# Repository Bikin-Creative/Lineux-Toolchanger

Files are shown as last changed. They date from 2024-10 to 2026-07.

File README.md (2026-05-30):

# Lineux-Toolchanger
### Toolchanger for fdm 3d printers
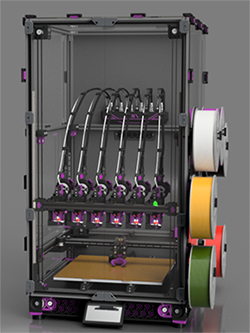
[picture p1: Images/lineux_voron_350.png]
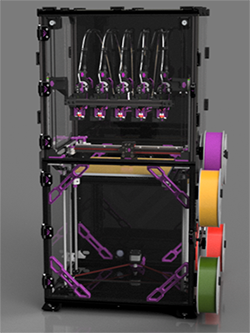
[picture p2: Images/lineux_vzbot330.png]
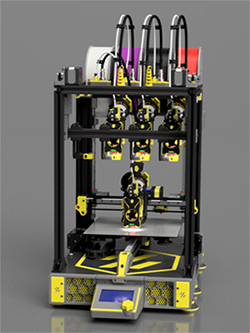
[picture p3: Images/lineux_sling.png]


# Discord
Our Discord server can be found here:

Discord Banner 2 (https://discord.gg/Xwqbjj4VjH)

# Description
Lineux Toolchanger consist of a suite of 3 parts:
1. Lineux - The hardware consisting of the Carriage, Toolhead and Dock
2. Btc - The macros handling the toolchange
3. Dockslide - Stowable dock to maximise print build

All 3 parts can be used with other systems. Example, Lineux can be used with other toolchanger plugin. Other toolchanger hardware can use Btc macros. Etc...

Lineux has evolved into a front mounted Toolchanger with Dockslide as our primary configuration.
If you intend to use a fixed dock configuration, pls do check or ask in discord if there are any mods or alternatives that may have already been released.

(Design, hardwares and configuration may change. Do check with us on discord)

# Is This Project for You?

This project is for makers and tinkerers who want to explore custom multi-tool 3D printing solutions.

If you’re simply looking for a plug-and-play machine, there are other great options available:

### Manufacture-ready toolchanger printers:
[Prusa XL](https://www.prusa3d.com/en/product/original-prusa-xl-semi-assembled-5-toolhead-3d-printer)

### Other DIY toolchanger projects:

[Stealthchanger](https://github.com/DraftShift/StealthChanger)

[Tapchanger](https://github.com/viesturz/tapchanger)

[Madmax](https://github.com/zruncho3d/madmax)

# All derivatives belong to their respective owners.<br/>
[Voron](https://github.com/vorondesign)<br/>
[Vzbot](https://github.com/VzBot3D)<br/>
[Voron CNC Carriage](https://github.com/Vitalii3D-xyz/VoronLightweightXCarriage)<br/>
[Voron Fysetc CNC Tap](https://github.com/FYSETC)<br/>

## Cost
Aside from costs at BOM, you will need these items. These are not included in the BOM
1. PSU. You will need 120W power for every tool. 6 tools will need 720W
2. Toolboard. Every tool will need 1 toolboard, eg [Fysetc H36](https://www.fysetc.com/cdn/shop/files/1_7592a53e-6f52-4a15-aeb8-11dbfa196516.jpg?v=1744444741)
3. Extruder. Every tool will need 1 extruder
4. Hotend. Every tool will need 1 hotend, eg [E3D Revo Voron](https://e3d-online.com/), [Trianglelab CHC](https://trianglelab.net/)
5. PDB. Although not really required, we recommend you to have a Power Distribution Board to provide connections/power to the toolboards, eg [Fysetc Tool Distribution Board](https://www.fysetc.com/cdn/shop/files/a3c4612ef030bc35ada3147286ebf6aa_b0e6d879-f14f-4daf-94f8-5ec51c08036b.jpg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)

# BOM
BOM is [here](https://github.com/Bikin-Creative/Lineux-Toolchanger/tree/main/BOM)

Lineux bom kit by fysetc is also available for purchase (Take note Bom kit is for previous r2.1 version)
[Lineux Kit](https://www.aliexpress.com/item/1005009944459058.html)

# Current stage
Lineux: Released

BTC: Released

Dockslide: Released

Dockslide project was kindly supported by ([Blurolls](https://www.blurolls3d.com) and [LDO Motors](https://ldomotors.com/))

# Instructions
Instructions/Guides are [here](https://github.com/Bikin-Creative/Lineux-Toolchanger/tree/main/Manual)

# If you would like to support our project
### [Ko-fi](https://ko-fi.com/lineux_toolchanger) ###

# Videos

https://github.com/user-attachments/assets/762defa3-31b9-4971-9426-da4857a4f154

https://github.com/user-attachments/assets/436ea148-65da-4729-8020-6bcd89354991

https://github.com/user-attachments/assets/d4576c4a-1339-4d5b-b265-4488fd4a67e5

# Prints

Printed by art on voron 2.4

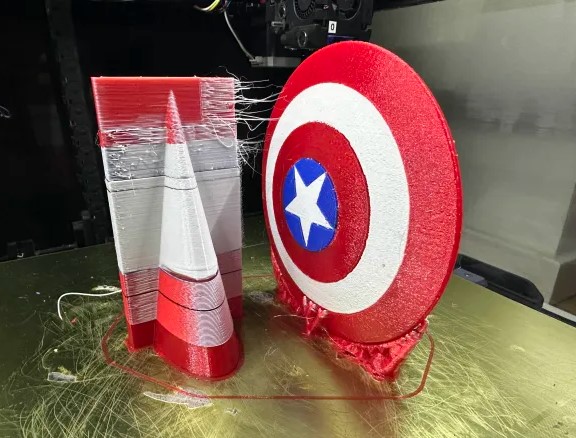
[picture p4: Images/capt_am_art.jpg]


Printed by 3dfiy My Life on vzbot330

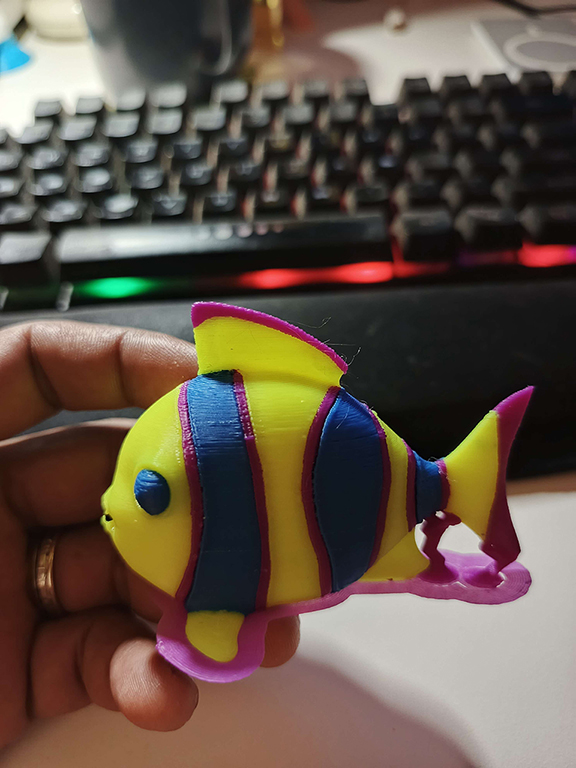
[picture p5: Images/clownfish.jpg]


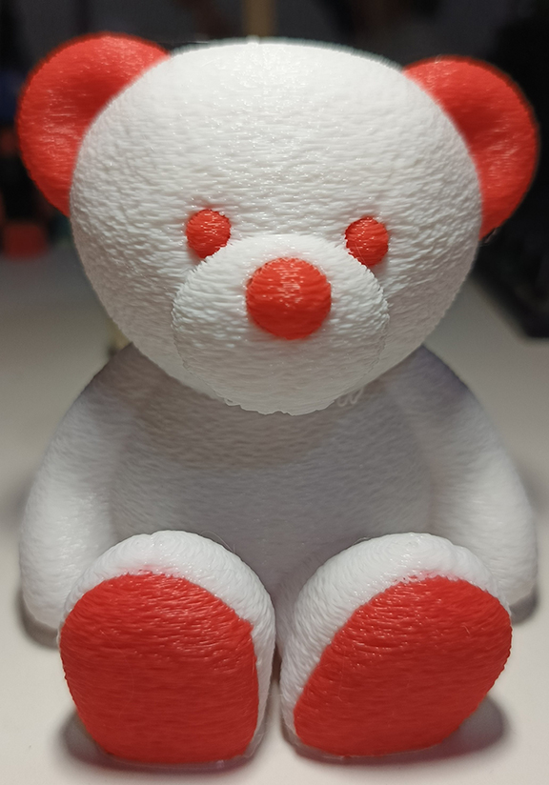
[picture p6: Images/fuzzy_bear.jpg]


Printed by guy on ratrig vcore3

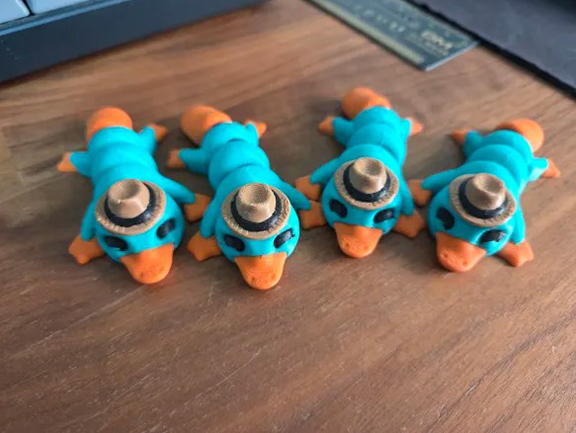
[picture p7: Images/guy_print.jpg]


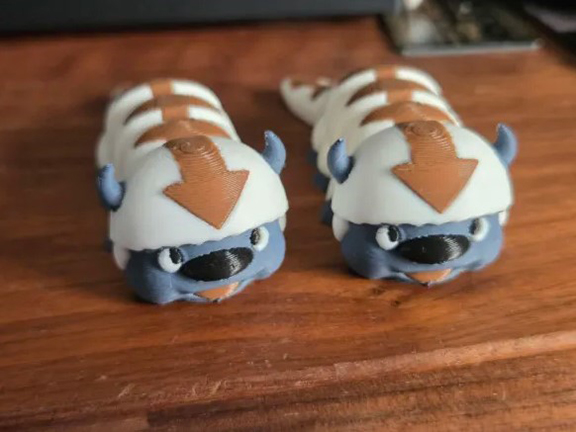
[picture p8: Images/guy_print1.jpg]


Printed by camtab on vzbot330

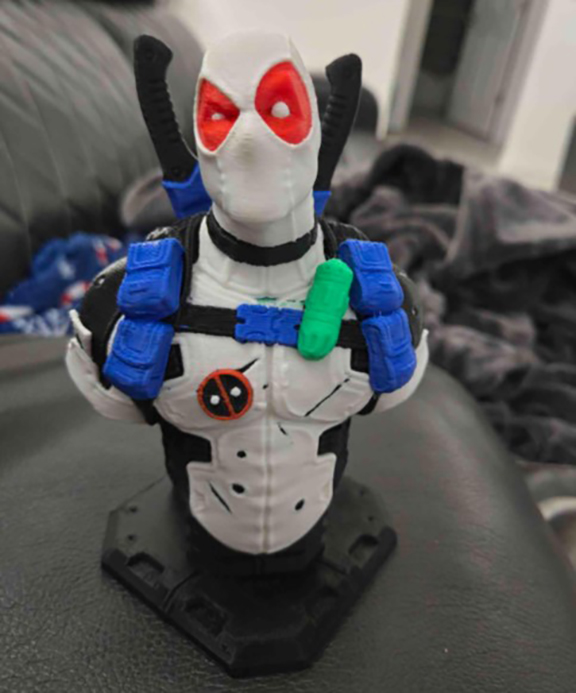
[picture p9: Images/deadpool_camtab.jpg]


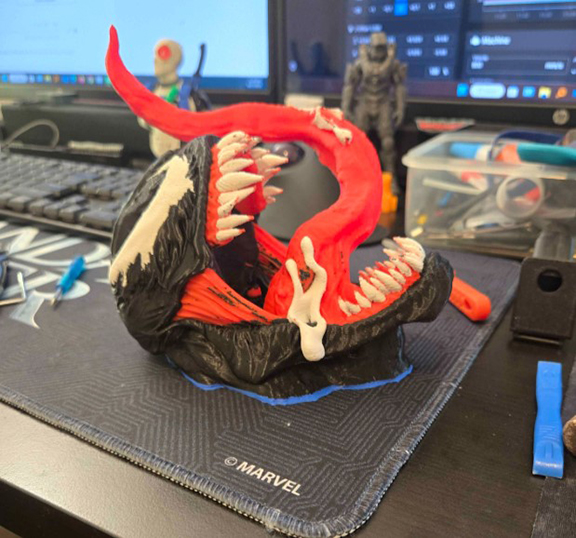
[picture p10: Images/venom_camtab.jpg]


# Printers
This project was developed on a Vzbot 330 and Voron 2.4. Other printers would need slight modifications. We could add support for other printers when there are others who had modded successfully, or when
we are able to get a hold of other printers to mod.

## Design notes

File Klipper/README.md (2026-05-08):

# Overview
Bikin Toolchanger is using pure macros. It uses snippets of codes from the [Magswitch](https://github.com/jera-sea/MagSwitch-Toolchanger) project and the
[Klicky Probe](https://github.com/jlas1/Klicky-Probe).

# Nozzle Offset Calibration Tool
You can use Tubby, Nudge, camera calibration or manual calibration. 
Nudge tool was created by [zruncho](https://github.com/zruncho3d/nudge). It provides a very accurate and convenient way to align nozzles for toolchangers.
Btc provide macros to utilize the tool for nozzle alignment. Instructions for use are [here](https://github.com/Bikin-Creative/Lineux-Toolchanger/blob/main/Manual/NUDGE.md).

# Macro Status
Fully tested and working. Released.

TODO:
1. Crash Detection

# Instructions
Instructions are [here](https://github.com/Bikin-Creative/Lineux-Toolchanger/blob/main/Manual/KLIPPER.md)

# Files
1. btc.cfg <- Main file, required
2. btc_variables.cfg <- Variables, required
3. tool_x.cfg <- Individual tool settings, required
4. bashed_macros.cfg <- For stress testing of toolchanger, required after set up
5. btc_nudge.cfg <- Macros for nudge tool, required during nozzle offset calibration set up
6. btc_extras <- Sample macros to use in start/end print and homing override
7. dockslide.cfg <- Required if using dockslide

# Video guide

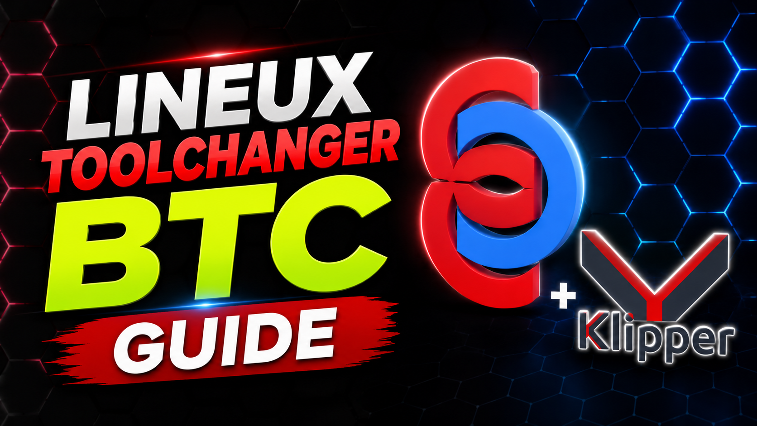
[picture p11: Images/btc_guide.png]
IMAGE ALT TEXT HERE (https://youtu.be/QYzVRNqW2J0?si=Q4HBHzA9LW7UP1U8)


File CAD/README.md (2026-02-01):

# Overview

## Lineux Stealth (Latest Release)
All cads released are based on a Voron 2.4 and Vzbot. You might need to adapt the dock and carriage to yr own printers. You can also check usermods section for any other printers cad/stl that may have been contributed by the community if they are not available here. Pls also do check in discord for any mods/contributions by the community.

Designs, mechanism and bom do get updated as we progress. Do take note. (It's a good practice to ask before committing to the build as design and hardwares may change)

# Printed Parts
Ensure the printed parts are printed without any warping to ensure proper and perfectly aligned components during installation.

It is recommended to do a test print on a small part for fitting, material shrinkage and tolerance measurement before commiting to the full printed parts.

Recommended slicer settings are as follows (Props to Voron team):
```
Layer height: 0.2mm
Extrusion width: 0.4mm, forced
Infill pecentage: 40%
Infill type: Adaptive Cubic, grid, gyroid, honeycomb, triangle, or cubic
Wall count: 4
Solid top/bottom layers: 5
```

# Carriage
Refer to the printer carriage available or check under usermods section. Pls do check in discord as well. All carriages are designed to be front facing and utilising Dockslide.

# Toolhead
Lineux R2T and EVA toolheads do not include onboard part-cooling fans. Instead, a single 5015 part-cooling fan mounted on the carriage is required.

Anthead and Dragonburner toolheads have their own onboard part-cooling fans, so a 5015 fan on the carriage is not needed when using these toolheads.

If you choose to have a mixture of toolheads in your setup, you should retain the 5015 carriage-mounted fan and use the multi-tool duct for part cooling.

# Docks
We recommend using Dockslide, as it allows you to use a single optimized dock design for both VzBot and Voron carriages.

If you are not using Dockslide, you will need to select the appropriate dock from the Fixed Dock files to match your specific carriage.

# Dockslide
Dockslide is a moving dock system to recover back any build volume loss encountered when having a fixed dock on the existing printer in which the frame wasn't extended in X or Y.

# Requirement
1. Carriage
2. Toolheads (Quantity depends on how many you require or may fit on yr printer. Minimum of 2 toolheads recomended)
3. Docks (1 dock per toolhead required)
4. Dockslide (You will need a fixed dock mount if you are not using dockslide)
5. Tubby (Required for tool nozzle offset calibration)

Join our [Discord](https://discord.gg/Xwqbjj4VjH) for any questions u may have. Let's go...

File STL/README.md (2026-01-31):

# Overview

# Printed Parts
Ensure the printed parts are printed without any warping to ensure proper and perfectly aligned components during installation.

It is recommended to do a test print on a small part for fitting, material shrinkage and tolerance measurement before commiting to the full printed parts.

Recommended slicer settings are as follows (Props to Voron team):
```
Layer height: 0.2mm
Extrusion width: 0.4mm, forced
Infill pecentage: 40%
Infill type: Adaptive Cubic, grid, gyroid, honeycomb, triangle, or cubic
Wall count: 4
Solid top/bottom layers: 5
```

# Printing Orientation
Normal auto rotate will work for all parts for proper printing orientation. 
These listed parts below however is recommended to be forced in the displayed printing orientation

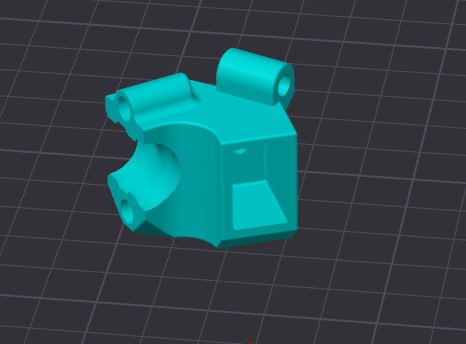
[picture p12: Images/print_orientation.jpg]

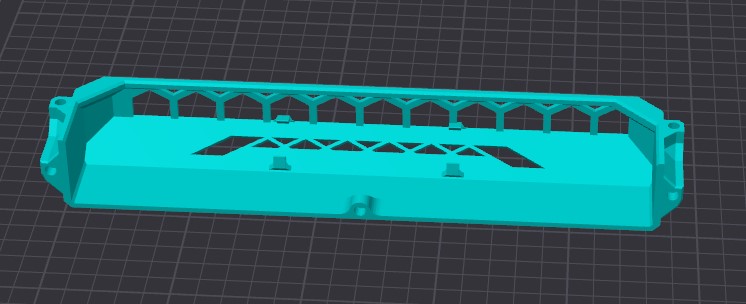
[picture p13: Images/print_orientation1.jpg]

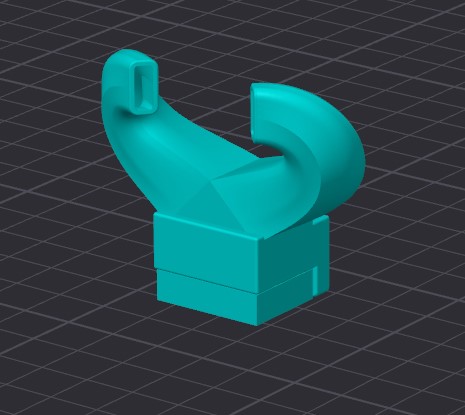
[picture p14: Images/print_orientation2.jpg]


Join our [Discord](https://discord.gg/Xwqbjj4VjH) for any questions u may have. Let's go...

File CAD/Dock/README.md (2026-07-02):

# Docks

The base Lineux design uses Dockslide, which provides the most optimized setup for running Lineux on your printer.

If you are using Dockslide, or if you are using fixed docks on a flying gantry printer, you may use the dockslide dock files.

If you are not using Dockslide, or if Lineux is installed on a non-flying gantry printer where the docks are mounted directly to the printer frame, you will need to use the fixed dock files that match your specific printer carriage.

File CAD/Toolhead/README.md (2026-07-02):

# Toolheads

Currently, Tiga Toolhead is our latest toolhead supported by Lineux.<br/>
The image specifications below may help you estimate how many toolheads can be installed on your printer.<br/>
There are some toolheads which have been modded to be compatible with Lineux Stealth. You can file their step files in the archive folder.<br/>

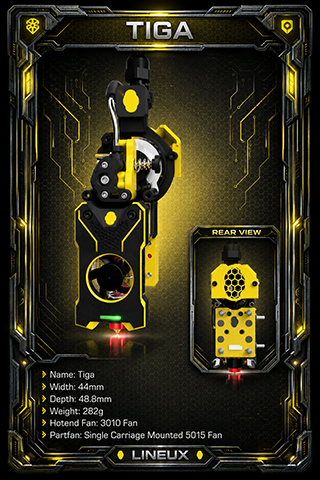
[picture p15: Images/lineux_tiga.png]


Join our [Discord](https://discord.gg/Xwqbjj4VjH) for any questions u may have. Let's go...

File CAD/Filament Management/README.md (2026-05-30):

# Filament Management

Currently, the maximum number of toolheads supported using Tiga is 6 toolheads on a Voron 2.4 R2 350, 5 toolheads on a VzBot 330 and 4 toolheads on Lineux Sling.

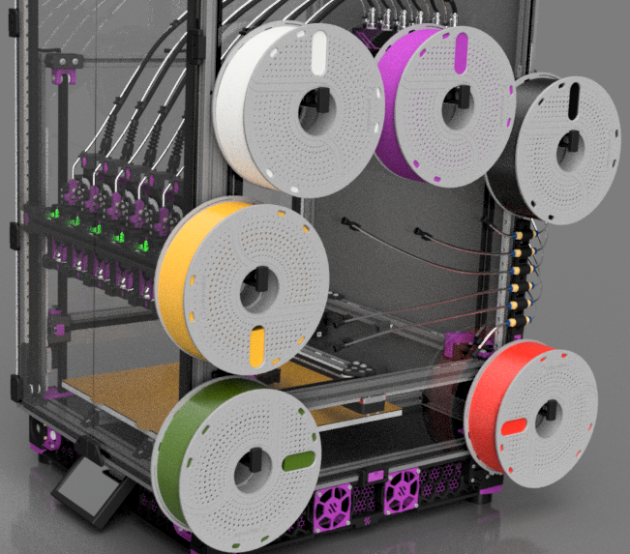
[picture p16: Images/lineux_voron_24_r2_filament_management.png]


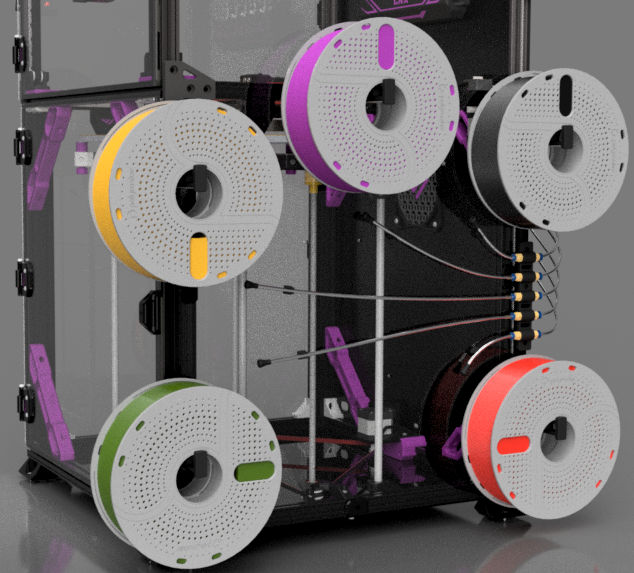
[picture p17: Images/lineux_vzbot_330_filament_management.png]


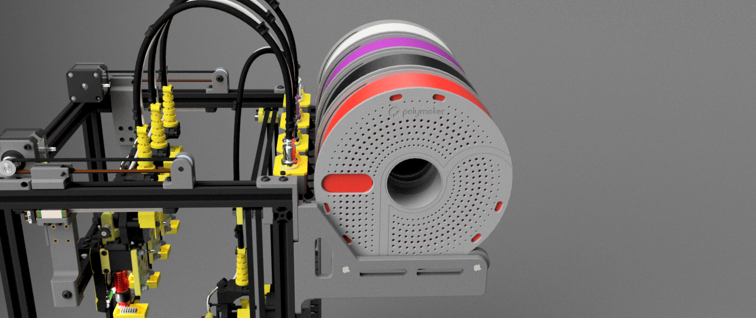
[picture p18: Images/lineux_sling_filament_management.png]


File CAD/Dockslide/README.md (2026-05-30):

# Dockslide
Dockslide is an optional addon to recover back any build volume loss encountered when having a fixed dock location on the existing printer.

# Thanks to Peter from Blurolls for providing the initial parts and components for the development of Dockslide. Also a big thanks to Jason from LDO for providing us with a higher torque motors.

# BOM
You can get the bom [Here](https://github.com/Bikin-Creative/Lineux-Toolchanger/tree/main/BOM)

Pls do not hesitate to ask any questions regarding the Dockslide on our discord channel.



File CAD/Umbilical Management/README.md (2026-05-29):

# Umbilical Management
Included in the CAD are Umbilical Hub (UmbiHub) mounts for 5-tool and 6-tool configurations.

The Nexus Box is designed to house toolhead distribution boards and supports either two [BTT CEB boards](https://github.com/bigtreetech/CEB)
or one [Fysetc Tool Distribution Board](https://github.com/FYSETC/Tool-Distribution-Board)<br/><br/>

This will enable cleaner wirings for your umbilicals from your toolheads to your MCU.<br/><br/><br/>
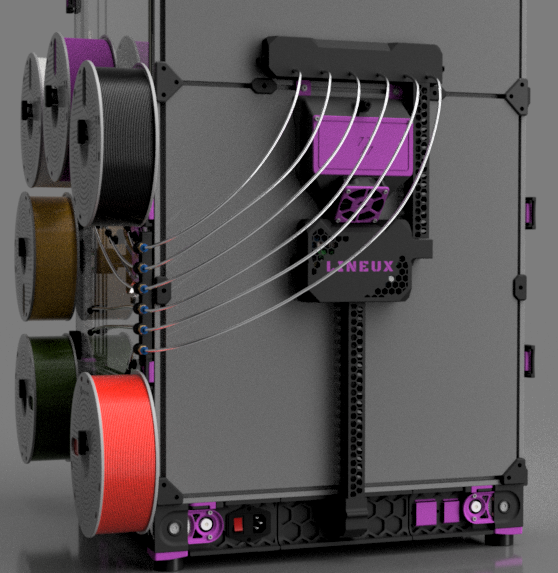
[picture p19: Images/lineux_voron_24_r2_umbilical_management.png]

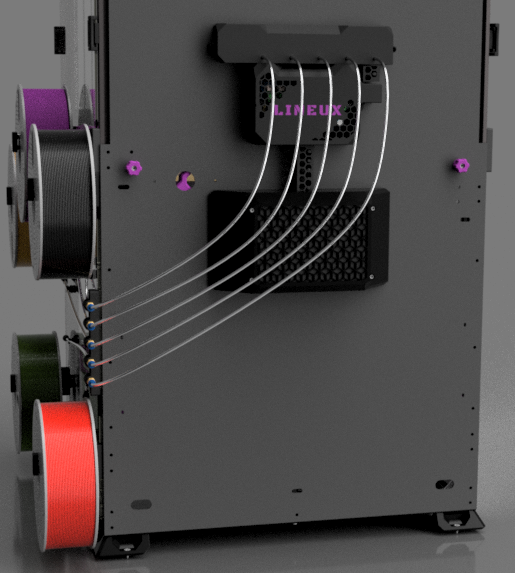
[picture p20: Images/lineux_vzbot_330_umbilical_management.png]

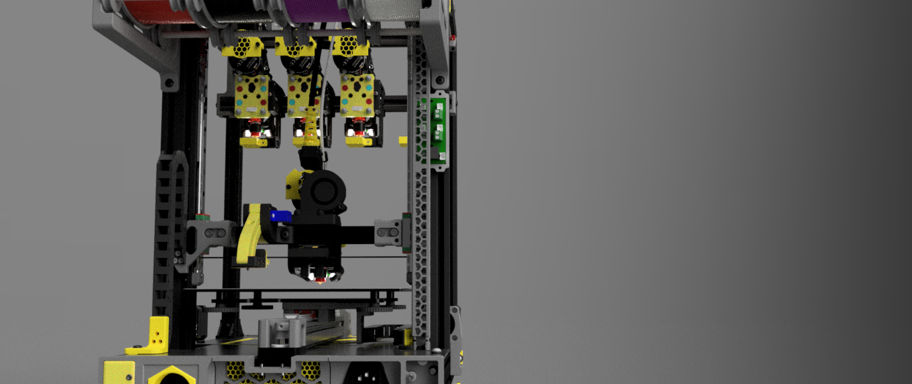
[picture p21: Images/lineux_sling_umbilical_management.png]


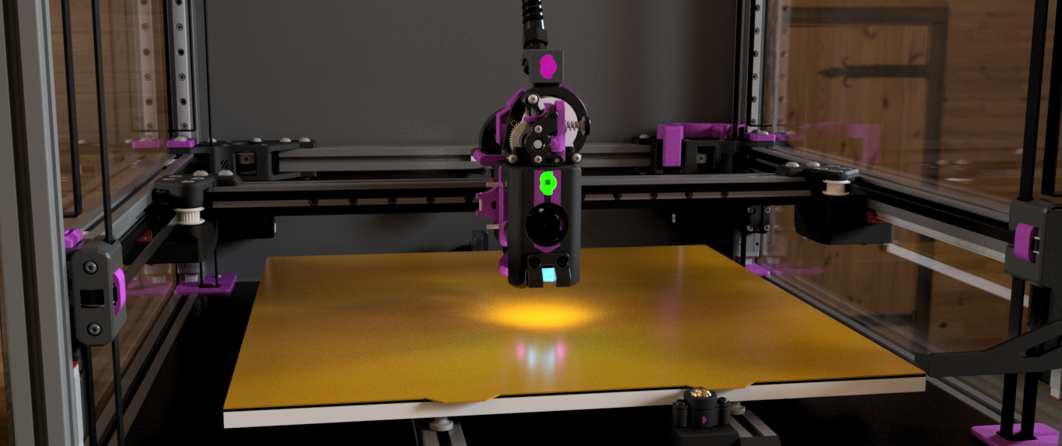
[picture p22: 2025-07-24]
Images/one_2.4.png

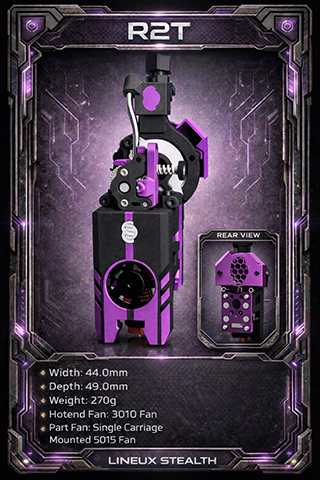
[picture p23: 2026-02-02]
Images/r2t.png

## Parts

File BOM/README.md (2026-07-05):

BOM difference between latest Lineux Stealth and current Fysetc Lineux r2.1 BOM Kit
<br/><br/>

Voron Carriage<br/>
m3x5x4 brass insert (10 instead of 12)<br/>
m3 hex nut (additional 2)<br/>
m3 x 6mm bhcs (not required)
m3 x 6mm fhcs (additional 2)
m3 x 6mm shcs (additional 4)
m3 x 8mm shcs (6 instead of 4)<br/>
m3 x 10mm shcs (not required)<br/>
m3 x 12mm fhcs (additional 2)<br/>
m3 x 12 shcs (additional 1)<br/>
m3 x 20mm bhcs (2 instead of 4)<br/>
spring OD6 ID5 10mm (not required)<br/>
AAA Battery Terminal 10x9mm (additional 2)
<br/><br/>

Vzbot Carriage<br/>
m3x5x4 brass insert (13 instead of 14)<br/>
m3 hex nut (additional 2)<br/>
m3 x 6mm fhcs (additional 1)<br/>
m3 x 10mm shcs (4 instead of 8)<br/>
m3 x 12mm bhcs (additional 2)<br/>
m3 x 12mm fhcs (additional 2)<br/>
m3 x 20mm shcs (additional 1)<br/>
m3 x 25mm bhcs (additional 1)<br/>
m3 x 35mm bhcs (additional 1)<br/>
m3 x 45mm bhcs (not required)<br/>
m3 dowel 35mm (35mm instead of 30mm)<br/>
spring OD6 ID5 10mm (not required)<br/>
AAA Battery Terminal 10x9mm (additional 2)
<br/><br/>

Toolhead<br/>
m2 x 8mm self-tap screw (additional 2)<br/>
m3x5x4 brass insert (additional 10)<br/>
m3 x 6mm bhcs (additional 4)<br/>
m3 x 8mm bhcs (2 instead of 4)<br/>
m3 x 8mm fhcs (additional 2)<br/>
m3 x 8mm shcs (additional 2)<br/>
m3 x 10mm bhcs (not required)<br/>
m3 x 10mm shcs (additional 5)<br/>
m3 x 20mm bhcs (not required)<br/>
m3 x 20mm shcs (additional 4)<br/>
m3 x 30mm shcs (additional 1)<br/>
m3 x 35mm bhcs (not required)<br/>
m3 x 35mm shcs (additional 4)<br/>
6 x 3mm n52 magnet (2 instead of 10)<br/>
Dupont Connector 3pin male and female (additional 1 pair)<br/>
Dupont Connector 6 pin male and female (additional 1 pair)<br/>
Microswitch (additional 1)<br/>
PG7 Flex Cable Gland (not required)<br/>
<br/><br/>

Dock<br/>
m3x5x4 brass insert (additional 3)<br/>
m3 x 6mm bhcs (additional 4)<br/>
m3 x 10mm bhcs (1 instead of 2)<br/>
m3 washer (additional 1)<br/>
6 x 3mm n52 magnet (4 instead of 5)<br/>

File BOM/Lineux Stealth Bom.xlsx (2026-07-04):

Lineux Stealth Bill Of Material
Bom subjected to changes based on feedbacks and hardware availability.
You may self-source or purchase the complete bom kit from Fysetc. (Not updated latest version yet)
All links are non affiliated. Links are provided as a reference to check the hardware dimensions, visual, etc.
Fysetc Lineux r2.1 Kit | https://www.aliexpress.com/item/1005009944459058.html |  | Currently Bom kit is for previous Lineux r2.1 (*Take Note*)
Lineux Stealth Voron Carriage | Quantity | Description | Source link | Remarks
m3x5x4 brass insert | 10
m3 hex nut | 2
m3 x 6mm fhcs | 2
m3 x 6mm shcs | 4
m3 x 8mm shcs | 6
m3 x 12mm fhcs | 2
m3 x 12mm shcs | 1
m3 x 20mm bhcs | 2
m3 dowel 14mm | 1 |  | link (https://www.aliexpress.com/item/4000473863693.html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)
m3 dowel 35mm | 1 |  | link (https://www.aliexpress.com/item/4000473863693.html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)
6 x 3mm n52 magnet | 4
8 x 5mm n52 magnet | 4
OD5 ID3 15mm SS Bushing | 1 | 3x5x15mm | link (https://www.aliexpress.com/item/1005008495477970.html)
OD8 ID6 3mm SS Bushing | 4 | 6x8x3mm | link (https://www.aliexpress.com/item/1005008532790703.html)
AAA Battery Terminal 10x9mm | 2 | Take note of the dimensions | link (https://www.aliexpress.com/item/32870772743.html?curPageLogUid=wDN6EM6N17D1) | Normally comes in pair but you only need the ones with spring.
jst xh2.54 connector 2pin female | 1 |  |  | Refer to cad if unsure which is female
5015 blower fan 24V 50mm wire | 1 |  | link (https://www.fysetc.com/products/5015-dc-24v-turbo-cooling-fan-for-blv-voron2-4-sb-vzbot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)
cable tie | 3
Lineux Stealth Vzbot Carriage | Quantity | Description | Source link | Remarks
m3x5x4 brass insert | 13
m3 hex nut | 2
m3 x 6mm fhcs | 1
m3 x 8mm shcs | 4
m3 x 10mm shcs | 4
m3 x 12mm bhcs | 4
m3 x 12mm fhcs | 2
m3 x 20mm bhcs | 2
m3 x 25mm bhcs | 1
m3 x 35mm bhcs | 1
m3 x 40mm shcs | 2
m3 dowel 14mm | 1
m3 dowel 35mm | 1 |  | link (https://www.aliexpress.com/item/4000473863693.html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)
6 x 3mm n52 magnet | 4
8 x 5mm n52 magnet | 4
OD5 ID3 15mm SS Bushing | 1 | 3x5x15mm | link (https://www.aliexpress.com/item/1005008495477970.html)
OD8 ID6 3mm SS Bushing | 4 | 6x8x3mm | link (https://www.aliexpress.com/item/1005008532790703.html)
AAA Battery Terminal 10x9mm | 2 | Take note of the dimensions | link (https://www.aliexpress.com/item/32870772743.html?curPageLogUid=wDN6EM6N17D1) | Normally comes in pair but you only need the ones with spring.
jst xh2.54 connector 2pin female | 1 |  | link (https://www.aliexpress.com/item/1005003422202370.html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) | Refer to cad if unsure which is female
5015 blower fan 24v | 1 |  | link (https://www.fysetc.com/products/5015-dc-24v-turbo-cooling-fan-for-blv-voron2-4-sb-vzbot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)
cable tie | 4
Lineux Stealth Tiga Toolhead | Quantity | Description | Source link | Remarks
m2 x 8mm self tap screw | 2
m3x5x4 brass insert | 23
m3 hex nut | 5
m3 x 6mm bhcs | 4
m3 x 8mm bhcs | 2
m3 x 8mm fhcs | 2
m3 x 8mm shcs | 2
m3 x 10mm shcs | 5
m3 x 20mm shcs | 4
m3 x 30mm shcs | 1
m3 x 35mm shcs | 4
m3 x 40mm bhcs | 1
m4x5x4 brass insert | 4
m4 cap nut | 4
m4 x 12mm set screw | 4 |  | link (https://www.aliexpress.com/item/4001081433504.html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)
6 x 3mm n52 magnet | 2
8 x 5mm n52 magnet | 4
m3 dowel 14mm | 2 |  | link (https://www.aliexpress.com/item/4000473863693.html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)
Dupont Connector 3pin Female | 1 |  |  | Only required if there's a probe on the toolhead.
Dupont Connector 6pin Female | 1
Dupont Connector 3pin Male | 1 |  |  | Only required if there's a probe on the toolhead.
Dupont Connector 6pin Male | 1
ws2812 Addressable Led | 3 |  | link (https://www.aliexpress.com/item/1005002055597390.html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)
microswitch 90deg | 1 |  | link (https://www.aliexpress.com/item/1005005596552328.html?scm_id=1007.40050.354490.0&scm-url=1007.40050.354490.0)
microswitch | 1
3010 axial fan 24v 150mm wire | 1 |  | link (https://www.fysetc.com/products/fysetc-1pcs-hydraulic-fan-24v-3010-extruder-fan-for-voron-0-2-3d-printer-accessories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)
Ring Terminal (RNB 1.25-3) | 2 |  | link (https://www.aliexpress.com/item/33031945048.html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) | You can also use the ones that comes with the ebb36 v1.2
Lineux Stealth Tiga Dock | Quantity | Description | Source link | Remarks
m3x5x4 brass insert | 4
m3 hex nut | 1
m3 x 6mm bhcs | 5
m3 x 10mm bhcs | 1
m3 washer | 2
m5 x 12mm bhcs | 4
m5 T-Nut | 4
6 x 3mm n52 magnet | 4
8 x 5mm n52 magnet | 2
m3 x OD4 16mm threaded dowel pin | 1 |  | link (https://www.aliexpress.com/item/1005005150593994.html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)
spring OD6 ID5 20mm | 1 | Length:20mm Wire Diameter:0.5mm Outer Diameter:6mm | link (https://www.aliexpress.com/item/1005007592875980.html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)
AA battery terminal 27x11mm | 1 | remove spring and drill hole to 3mm | link (https://www.aliexpress.com/item/1005003438264831.html?curPageLogUid=9sgHbNrWVcU1) | take note of the dimensions
Silicon Brush | 1 | cut to required length | link (https://www.fysetc.com/products/fysetc-nozzle-silicone-brush-using-for-bambu-labs-a1-3d-printer-accessories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)
Miscellaneous | Quantity | Description | Source link | Remarks
Loctite | 1 | For securing bolts to heat inserts or hex nuts. |  | optional
Super glue | 1 | For securing magnets.
Quick Set Clear Epoxy | 1 | For securing magnets. |  | optional

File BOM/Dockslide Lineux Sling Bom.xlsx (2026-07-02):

Lineux Sling Bill Of Material
Bom subjected to changes based on feedbacks and hardware availability.
All links are non affiliated. Links are provided as a reference to check the hardware dimensions, visual, etc.
Bom is for an Enderwire and doesn't include the Enderwire Printer itself.
Carrier, Lock Plate, Dock and Servo Klicky will require their respective bom.
Lineux Sling Carriage | Quantity | Description | Source link | Remarks
m3 heat insert | 14
m3 hex nut | 3
m3 x 6mm shcs | 6
m3 x 8mm shcs | 2
m3 x 20mm shcs | 4
m3 x 25mm bhcs | 2
m3 x 40mm shcs | 3
6x3mm magnet | 4 | 2 for klicky
5015 Radial Fan | 1
Lineux Sling Dockslide | Quantity | Description | Source link | Remarks
2020 Extrusion 290mm | 3
2020 Extrusion 320mm | 1
2020 Extrusion 420mm | 2
MGN 9C + 120mm rail | 2
m3 heat insert | 10
m3 x 6mm shcs | 8
m3 x 8mm shcs | 20
m3 x 10mm shcs | 16
m3 x 20mm shcs | 2
m3 x 30mm shcs | 2
m5 x 8mm bhcs | 2
m5 x 10mm bhcs | 10
m5 x 20mm bhcs | 2
GT2 Pulley 20T W6 B5 | 2
GT2 Belt W6 400mm | 2
GT2 Idler 20T W6 B5 | 2
nema 17 stepper motor | 2 | LDO-42STH40-1684AC |  | Recommended Motor
Lineux Sling Umbilical Management | Quantity | Description | Source link | Remarks
m3 x 30mm shcs | 8
GX-16 Connector (male + female set) | 4
PC4 M10 Connector | 8
Lineux Sling Filament Management | Quantity | Description | Source link | Remarks
m5 x 10mm bhcs | 2
m5 x 15mm bhcs | 2
8mm lead screw 330mm | 2 |  |  | Can use rod as alternative

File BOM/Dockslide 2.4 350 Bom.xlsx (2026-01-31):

Dockslide 2.4 r2 350 Bill Of Material
Bom subjected to changes based on feedbacks and hardware availability.
Bom does not include panel clip/latch, door hinge and their respective hardwares.
Item | Quantity | Description | Source link | Remarks
2020 T-slot extrusion 880mm | 2 | Tophat height is 350mm |  | Use the calculator below to get the required front extrusion length and rail length. Tophat height may be affected by bed size and umbilical length.
2020 T-slot extrusion 490mm | 2
2020 T-slot extrusion 470mm | 2
2020 T-slot extrusion 400mm | 1
2020 T-slot extrusion 350mm | 2
MGN9C + Rail 550mm | 2
GT2 20T Pulley 9mm Belt ID5 | 2 |  |  | 10mm belt is fine too.
GT2 20T Toothed Idler 9mm Belt ID5 | 2 |  |  | 10mm belt idler is fine too.
Gates Belt 9mm 1.7metres | 2
Nema 17 Stepper | 2 | LDO-42STH40-1684AC |  | Recommended Motor
Micro switch | 2
m3 heat insert | 2 |  |  | m3xod5x4
m3 x 8mm bhcs | 8
m3 x 20mm bhcs | 2
m3 x 25mm shcs | 8
m3 x 40mm shcs | 2
m5 x 10mm bhcs | 18
m5 x 20mm bhcs | 2
2020 hidden corner bracket | 16 |  |  | If not using blind joints
2020 parallel joint | 4
2020 straight line joint | 2
Panels
Top 504 x 484mm | 1 | Transparent
Sides 504 x 344mm | 2 | Transparent
Back 484 x 344mm | 1 | Opaque
Door 241.5 x 853.5mm | 2 | Transparent
Dockslide Required Length Calculator
Description |  | Enter Length | Required Length | Remarks
Step 1. To calculate the required dockslide vertical extrusion length, enter yr printer front vertical extrusion length |  | 530 | 880 | Length may be affected by bed size and umbilical length.
Step 2. To calculate the required rail length, enter yr dockslide required vertical extrusion length |  | 880 | 550
Step 3. To calculate dock extrusion bar length, enter yr printer horizontal extrusion length |  | 470 | 400
Step 4. To calculate the maximum number of tools you can install, enter dock extrusion bar length |  | 400 | 6.00 | Round down number

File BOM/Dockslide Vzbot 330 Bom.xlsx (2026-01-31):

Dockslide Vzbot 330 Bill Of Material
Bom subjected to changes based on feedbacks and hardware availability.
Bom does not include panel clip/latch, door hinge and their respective hardwares.
Item | Quantity | Description | Source link | Remarks
2020 T-slot extrusion 480mm | 4 | Tophat height is 495mm
2020 T-slot extrusion 530mm | 2
2020 T-slot extrusion 460mm | 2
2020 T-slot extrusion 360mm | 1
MGN9H + Rail 250mm | 2
Hardware | Quantity | Description | Source link | Remarks
GT2 20T Pulley 9mm Belt ID5 | 2 |  |  | 10mm belt is fine too.
GT2 20T Toothed Idler 9mm Belt ID5 | 2 |  |  | 10mm belt idler is fine too.
Gates Belt 9mm 1 metre | 2
Nema 17 Stepper | 2 | LDO-42STH40-1684AC |  | Recommended Motor
Micro switch | 2
m3 heat insert | 2 |  |  | m3xod5x4
m3 x 8mm bhcs | 8
m3 x 20mm bhcs | 2
m3 x 25mm shcs | 8
m3 x 40mm shcs | 2
m5 x 8mm bhcs | 8 |  |  | For corner bracket
m5 x 10mm bhcs | 34
m5 x 20mm bhcs | 2
m5 t-nut | 8 |  |  | For corner bracket
2020 corner bracket | 4 |  |  | Optional For stiffness
2020 hidden corner bracket | 4 |  |  | Optional For stiffness
Panels
Top 503.5 x 473.5mm | 1 | Transparent
Sides 470.5 x 486.5mm | 2 | Transparent
Back 504.5 x 485mm | 1 | Opaque
Door 530 x 494.5mm | 1 | Transparent

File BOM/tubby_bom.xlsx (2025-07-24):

Tubby - Nozzle Offset Calibration Tool
6x3mm Floating Base | Quantity | Description
m3 x 6mm shcs | 1
m3 x 16mm bhcs | 2
m3 brass insert | 2
m3 x 8mm dowel | 1 | Solder a wire to one end of the dowel
12mm steel ball bearing | 1
6 x 3mm n35 magnet | 6 | n35 or lower
JST XH 2.1 Female | 1
8x5mm Floating Base | Quantity | Description
m3 x 6mm shcs | 1
m3 x 16mm bhcs | 2
m3 brass insert | 2
m3 x 8mm dowel | 1 | Solder a wire to one end of the dowel
12mm steel ball bearing | 1
6 x 3mm n35 magnet | 3 | n35 or lower
8 x 5mm n35 magnet | 3 | n35 or lower
JST XH 2.1 Female | 1
10x5mm Floating Base | Quantity | Description
m3 x 6mm shcs | 1
m3 x 16mm bhcs | 2
m3 brass insert | 2
m3 x 8mm dowel | 1 | Solder a wire to one end of the dowel
12mm steel ball bearing | 1
6 x 3mm n35 magnet | 3 | n35 or lower
10 x 5mm n35 magnet | 3 | n35 or lower
JST XH 2.1 Female | 1
Fixed Base | Quantity | Description
m3 x 15mm shcs | 1
m3 x 16mm bhcs | 2
m3 x 25mm shcs | 2
m3 brass insert | 2
m3 x 8mm dowel | 1 | Solder a wire to one end of the dowel
12mm steel ball bearing | 1
6 x 3mm n35 magnet | 3 | n35 or lower
JST XH 2.1 Female | 1

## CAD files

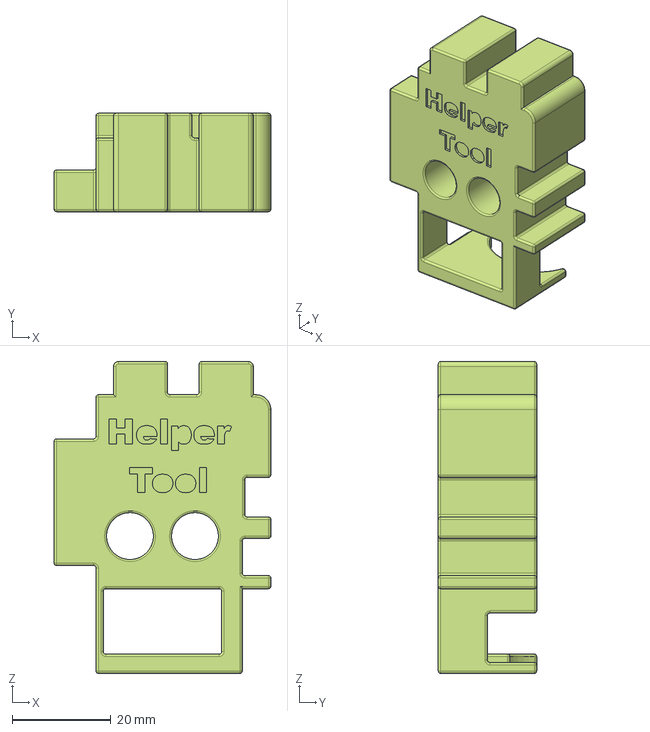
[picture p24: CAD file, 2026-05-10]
CAD/Assist Tool/Magnet Helper v9.step
44.0 x 20.0 x 63.3 mm

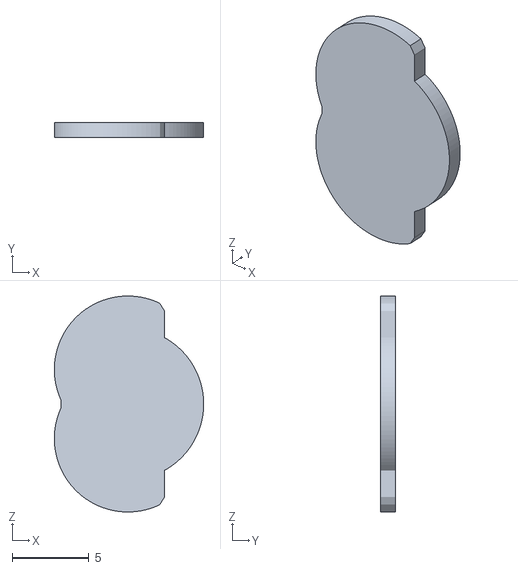
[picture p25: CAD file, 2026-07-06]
STL/Carriage/Enderwire Sling Carriage/[a]_lock_plate_logo.stl
9.75 x 1.00 x 14.1

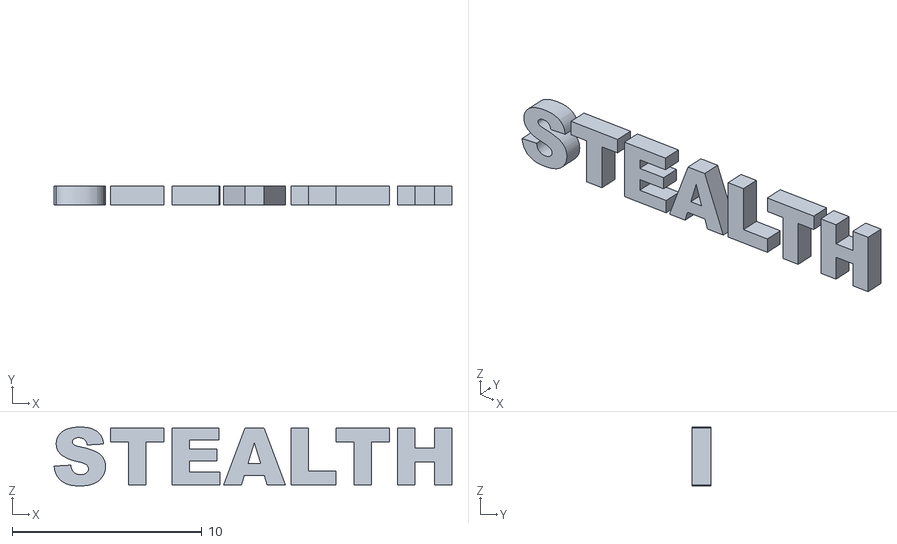
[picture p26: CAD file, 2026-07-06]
STL/Carriage/Voron CNC Carriage/[a]_carrier_trim.stl
21.0 x 1.00 x 3.10

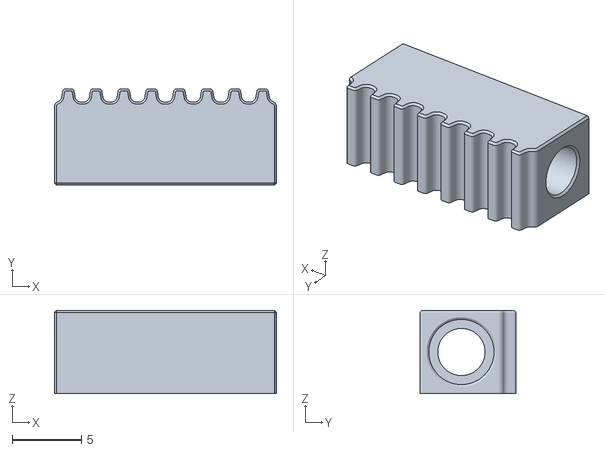
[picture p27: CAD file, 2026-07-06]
STL/Carriage/Vzbot/[a]_belt_tensioner_x2.stl
16.0 x 6.95 x 6.00

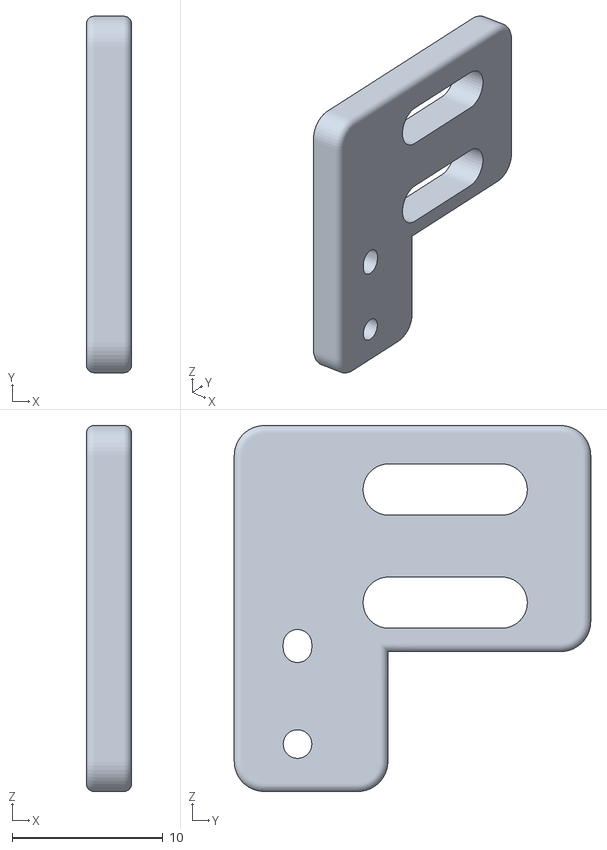
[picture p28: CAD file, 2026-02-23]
STL/Carriage/XY Endstop/Voron/y_switch_mount.stl
3.00 x 23.7 x 24.3

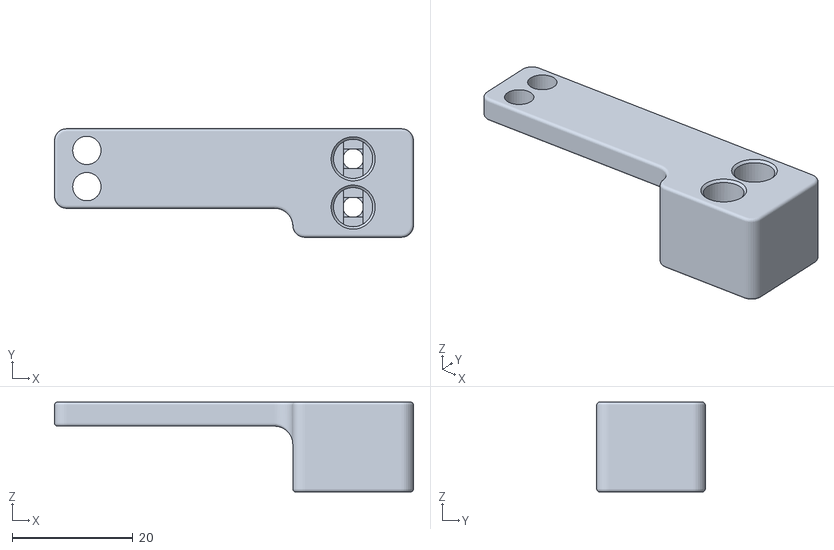
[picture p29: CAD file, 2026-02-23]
STL/Carriage/XY Endstop/Vzbot/x_endstop_mount.stl
59.5 x 18.0 x 14.9

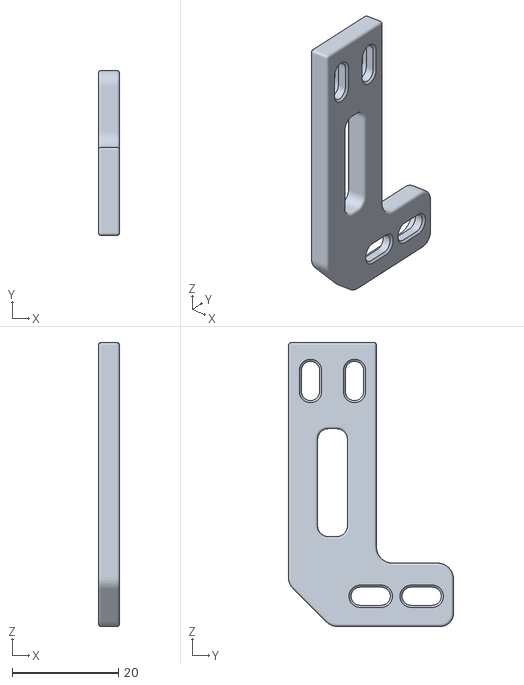
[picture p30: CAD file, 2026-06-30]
STL/Docks/Dockslide/spine_dock_nozzle_blocker_mount.stl
4.00 x 31.1 x 53.5

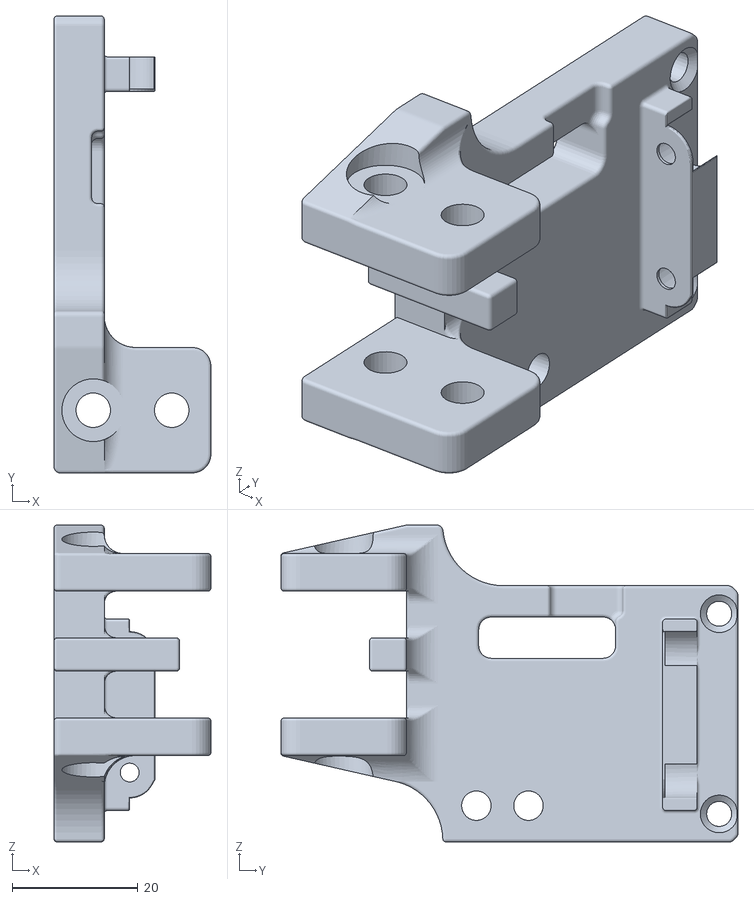
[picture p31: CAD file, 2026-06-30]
STL/Docks/Fixed Docks/dock_voron_printed.stl
25.0 x 72.8 x 50.5

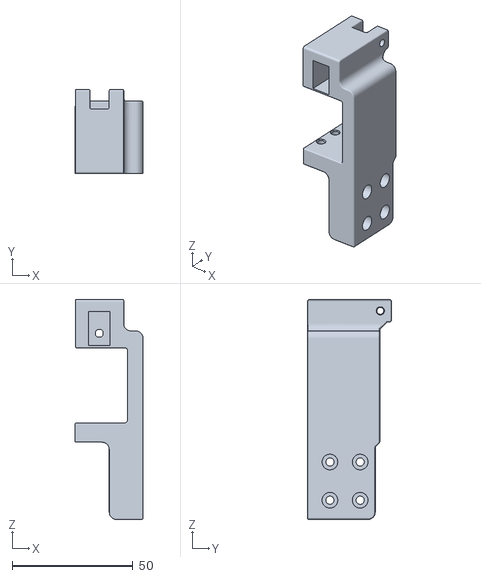
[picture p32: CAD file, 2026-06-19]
STL/Dockslide/Sling/dockslide_mount_left.stl
28.2 x 34.9 x 91.0

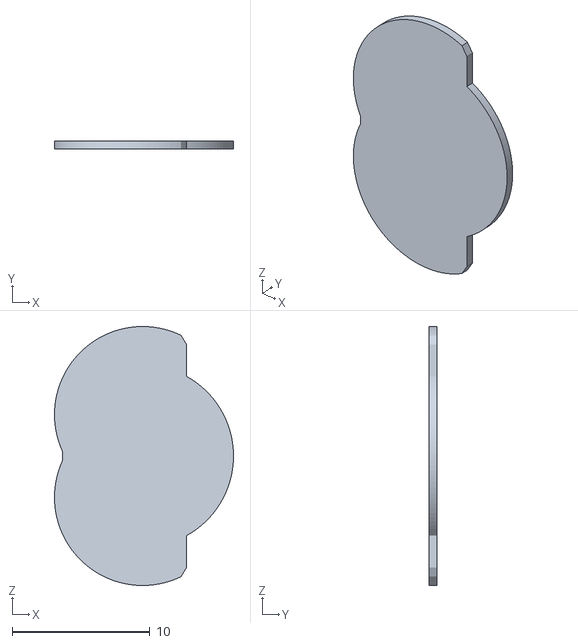
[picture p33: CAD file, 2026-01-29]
STL/Dockslide/Voron/Dockslide/Left/[a]_logo.stl
13.0 x 0.6 x 18.8

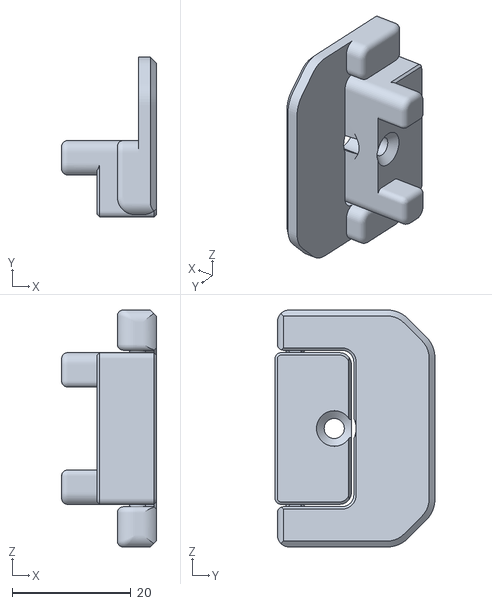
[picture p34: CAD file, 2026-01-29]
STL/Dockslide/Voron/Door/door_hinge.stl
16.0 x 27.0 x 40.0

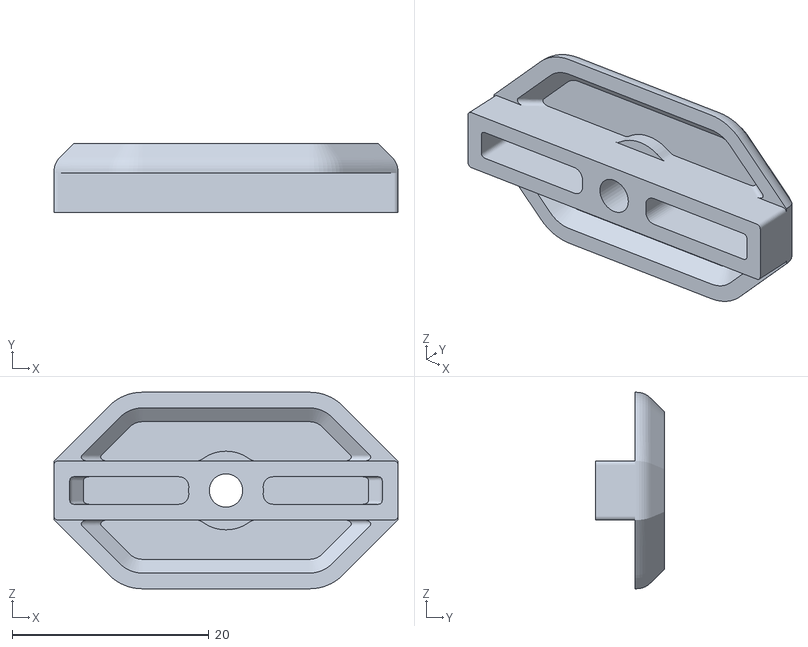
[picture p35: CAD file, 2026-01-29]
STL/Dockslide/Voron/Panel Clip/Rear Panel Clips Middle Sandwich.stl
35.0 x 7.00 x 20.0

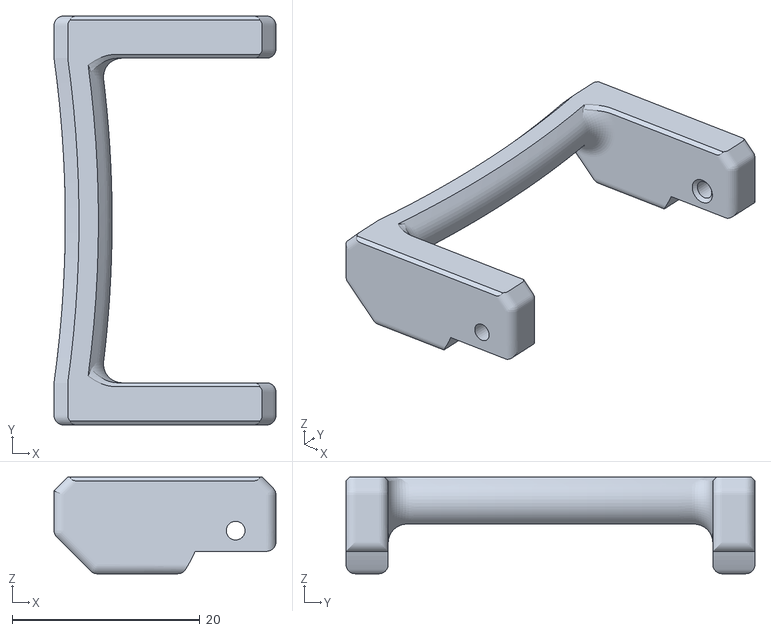
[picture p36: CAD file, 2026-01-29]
STL/Dockslide/Voron/Quick Release Latch/Latch Normal/Normal OuterHinge.stl
23.7 x 43.6 x 10.3

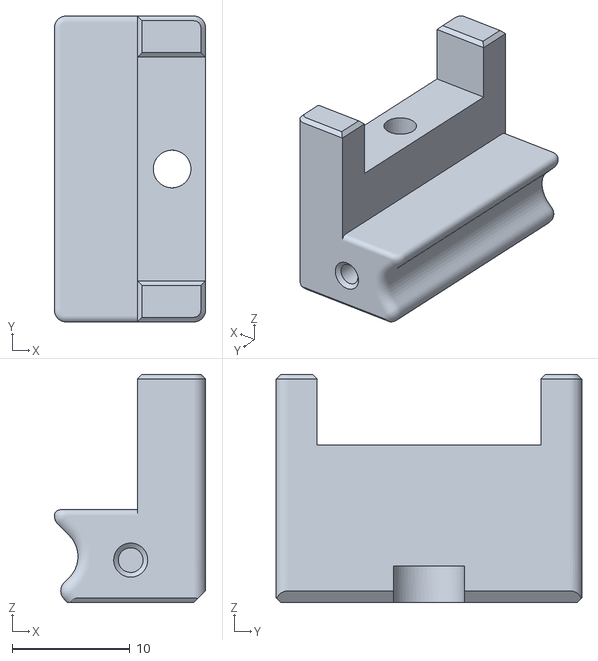
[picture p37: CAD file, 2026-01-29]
STL/Dockslide/Voron/Quick Release Latch/Latch Sandwich/Sandwich HingeBody.stl
12.8 x 26.0 x 19.4

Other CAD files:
STL/Assist Tool/magnet_helper.stl
STL/Carriage/Voron Printed Carriage/[a]_lock_plate_logo.stl
STL/Dockslide/Voron/Dockslide/Right/[a]_logo.stl
STL/Archive/Lineux Stealth Dock/Dockslide Docks/Anthead/[a]_drip_tray.stl
STL/Archive/Lineux Stealth Dock/Dockslide Docks/Anthead/[a]_logo_nb.stl
STL/Archive/Lineux Stealth Dock/Dockslide Docks/Anthead/anthead_dock.stl
STL/Archive/Lineux Stealth Dock/Dockslide Docks/Anthead/nozzle_blocker_mount.stl
STL/Archive/Lineux Stealth Dock/Dockslide Docks/Dragonburner/[a]_drip_tray.stl
STL/Archive/Lineux Stealth Dock/Dockslide Docks/Dragonburner/[a]_logo_nb.stl
STL/Archive/Lineux Stealth Dock/Dockslide Docks/Dragonburner/db_dock.stl
STL/Archive/Lineux Stealth Dock/Dockslide Docks/Dragonburner/nozzle_blocker_mount.stl
STL/Archive/Lineux Stealth Dock/Dockslide Docks/Eva/[a]_drip_tray.stl
STL/Archive/Lineux Stealth Dock/Dockslide Docks/Eva/[a]_logo_nb.stl
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

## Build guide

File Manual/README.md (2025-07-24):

# Toolhead Board Wiring Diagram

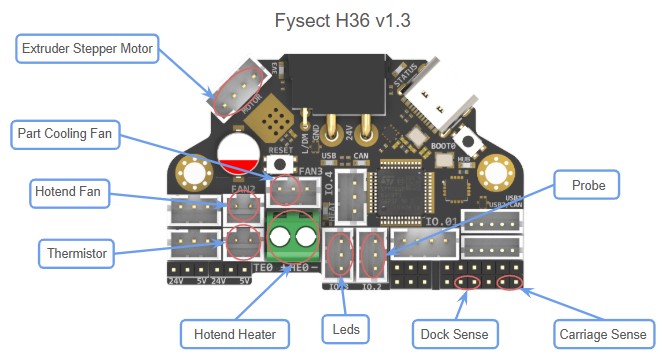
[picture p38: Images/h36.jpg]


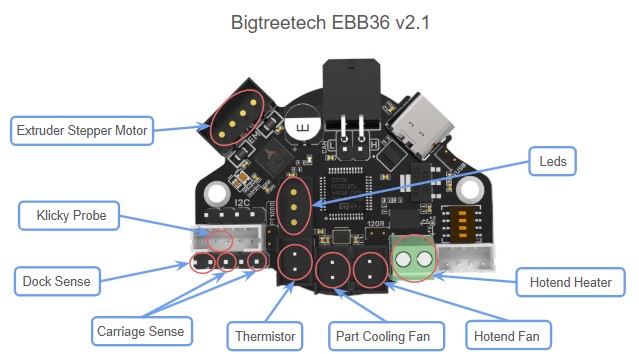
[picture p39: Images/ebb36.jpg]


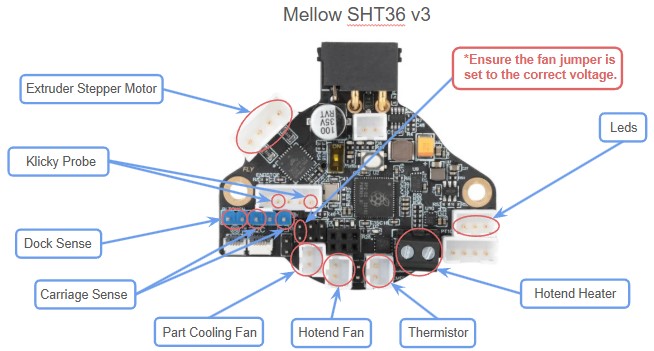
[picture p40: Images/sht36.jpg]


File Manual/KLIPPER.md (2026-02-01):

 1. Create new folder btc in config folder.
 2. Copy files into btc folder.
 3. Edit tool_0.cfg. Change all relevant sections pertaining to the toolhead/board.
 4. Optional, add more cfg for additional toolhead. For each additional toolhead, edit btc_variables.cfg to include the new tool_x.cfg files.
 5. Edit tool_x.cfg as per step 3.
 6. Firmware restart to verify all cfg are valid. Fix any error/s found before proceeding further.
 7. Edit all tool_x.cfg to set the toolhead pickup and dropoff movement.
 8. Edit tool_x.cfg to set the following:
    1. variable_pickup_approachlocation
    2. variable_pickup_moves
    3. variable_dropoff_approachlocation
    4. variable_dropoff_moves
    
       All moves are absolute move in mm.
 9. Firmware restart to verify all cfg are valid. Fix any error/s found before proceeding further.
10. Use ```Get_Tool_States``` buttons to test system senses. Go thru every toolhead. Make sure every toolhead report its location correctly.
    1. Put tool 0 to dock.
    2. Click ```Get_Tool_States```.
    3. Make sure it returns Tool 0: carriage:no dock:yes
    4. Now put tool at carriage and repeat the test. Make sure the test reports Tool 0: carriage:yes dock:no
    5. Do this test for all tools.
11. DO NOT proceed further if any tool fail the above test.
12. tbc

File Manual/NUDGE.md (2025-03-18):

# Instructions

Edit `btc_nudge.cfg` as below:

```
[gcode_button nudge_sensor_pin]
pin: ^PG15
press_gcode:
release_gcode:
# Enter pin number your nudge tool is connected to. Leave the rest as is.
```

```
[gcode_macro _nudge_variables]
variable_nudge_resolution: 0.05      # Resolution should be between 0.01 - 0.1
variable_nudge_travel_speed: 100
# resolution must be between 0.01 - 0.1. Probing will be very very slow at highest resolution of 0.01. For faster probing, use lower resolution of 0.1.
# travel_speed, set at your usual travel speed
```

Save and restart firmware.

Home All

Z Tilt/Quad Gantry

Home Z

Move nozzle to a position about center of probe, and about 3mm above probe

NUDGE_FIND_TOOL_OFFSETS

When done, retrieve all tools offsets from console as describe below:

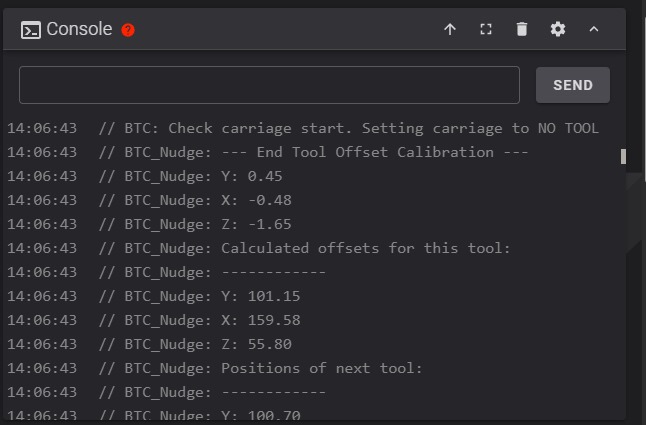
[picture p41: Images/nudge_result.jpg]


```
Calculated offsets for this tool:
Z: -1.65
X: -0.48
Y: 0.45
--- End Tool Offset Calibration ---
```

By using the numbers above, edit `tool_x.cfg` and enter these offsets. Scroll thru the console to get offsets for all tools.

# Video guide

IMAGE ALT TEXT HERE (https://www.youtube.com/watch?v=0_R_rUG1s-4&t=8s)

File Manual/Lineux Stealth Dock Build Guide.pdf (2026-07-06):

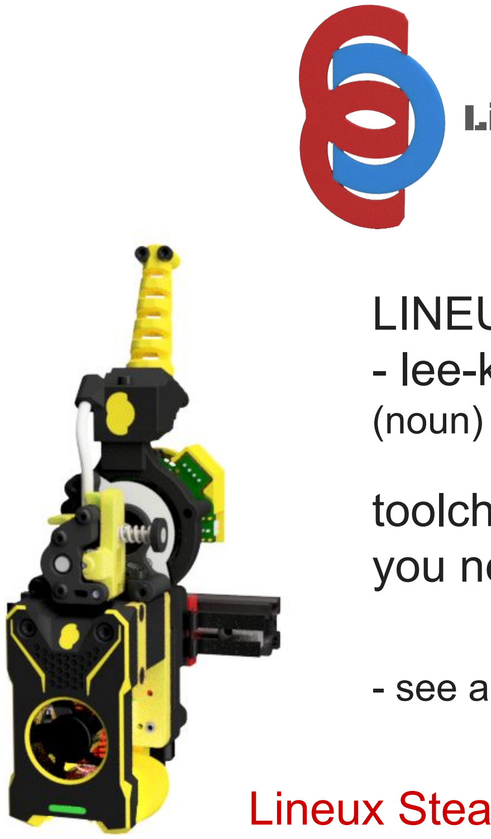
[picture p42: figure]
(noun)

## Lineux Toolchanger

## LINEUX - lee-knee-yurks

## toolchanger that print things you never know you need in a way you never imagine

### - see also wizardry, mesmerizing

## Lineux Stealth Dock Build Guide

06/07/2026

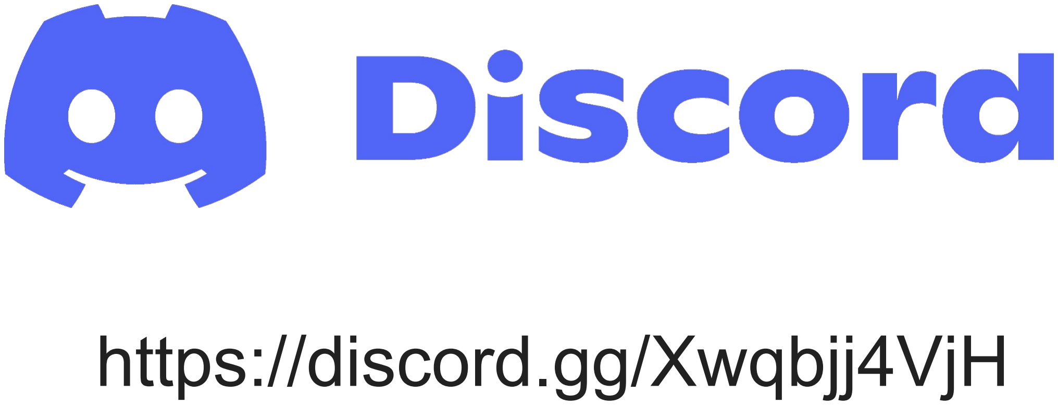
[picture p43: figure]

2 ________________________________________________________________________________________________________

## A big thank you to everyone who

made this project possible.

https://discord.gg/Xwqbjj4VjH | https://github.com/Bikin-Creative/Lineux-Toolchanger

If you like what we do, support us to keep us going.

________________________________________________________________________________________________________ 3

## CAUTION

- Please take careful precautions with safety in mind when attempting to build Lineux.
- Only attempt the build if you are knowledgeable with 3d printer mechanics and electronics.
- Failure to follow safety precautions may result in things going against you, or even harm you.
- Magnets are extremely strong and may cause injuries. Please handle them with extra care.
- If things start to get confusing or you’re stuck at some point during the build, do ask questions on our discord.
- We try to keep things as simple and as clear as possible for a fun and enjoyable build for everyone.
- We are humans and are prone to mistakes. If you encounter any issues/faults with the build guide, please raise them on our Discord.

Table Of Contents | https://github.com/Bikin-Creative/Lineux-Toolchanger

4 ________________________________________________________________________________________________________

Introduction | 05
Hardware | 07
Preparation | 09
Dock | 11
Spine Dock | 23
Completion | 38

Introduction | https://github.com/Bikin-Creative/Lineux-Toolchanger

________________________________________________________________________________________________________ 5

Part Printing Recommendations Recommended setting/material to print your parts.

Material
ABS

Layer Height
0.2mm

Extrusion Width
0.4mm

Infill
40% ( Grid, Gyroid, Honeycomb, Triangle, Cubic )

Number of Walls
4

Number of Top/Bottom
5

https://github.com/Bikin-Creative/Lineux-Toolchanger

6 ________________________________________________________________________________________________________

Introduction

Parts Filename Guide

Primary Colour

Eg. carriage_A.stl

These are to be printed
with your primary/base
colour.

Accent Colour

Eg. [a]_locking_plate.stl

Files with [a] in front are to be printed with your
secondary/accent colour.
Parts will be indicated
with the Lineux Logo
beside it in this guide.

Quantity Required

Eg. belt_tensioner_x2.stl

Files ending with x#
indicate the quantity
required to be printed

To make your build easier, we recommend you to download the cad from our github to enable you to visualize the whole assembly.

Hardware | https://github.com/Bikin-Creative/Lineux-Toolchanger

________________________________________________________________________________________________________ 7

Button Head Cap Screw
(BHCS)

Heat Insert

Socket Head Cap Screw
(SHCS)

n52 Magnet

T-Nut | Hex Nut

AA Battery Terminal

Threaded Dowel Pin

Washer

Compression Spring

Flat Head Cap Screw
(FHCS)

8 ________________________________________________________________________________________________________

Lineux is a derivative of 2 words, Linear and Flux.

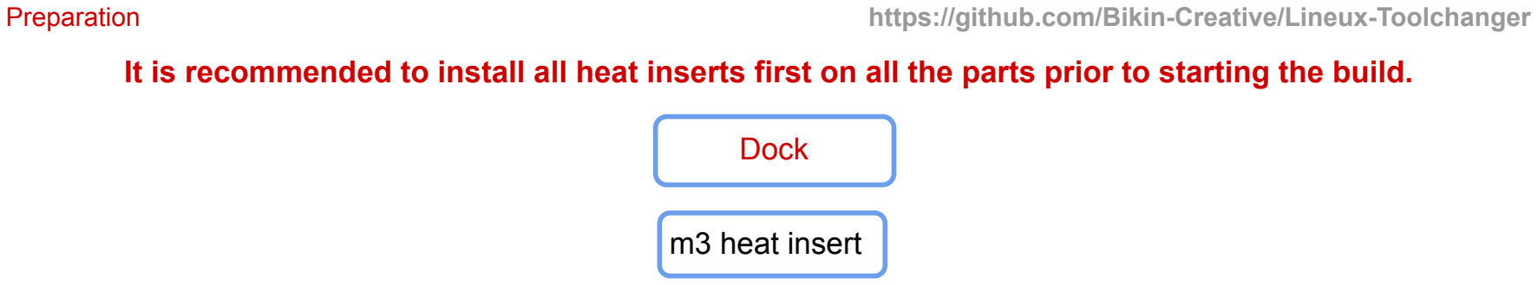
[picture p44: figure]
Preparation; Dock; m3 heat insert
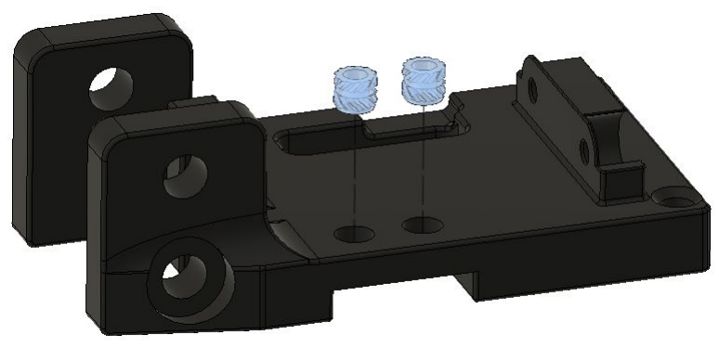
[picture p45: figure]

________________________________________________________________________________________________________ 9

It is recommended to install all heat inserts first on all the parts prior to starting the build.

Preparation
Insert the heat insert to the Dock Body and Nozzle Blocker.

Spine Dock

m3 heat insert

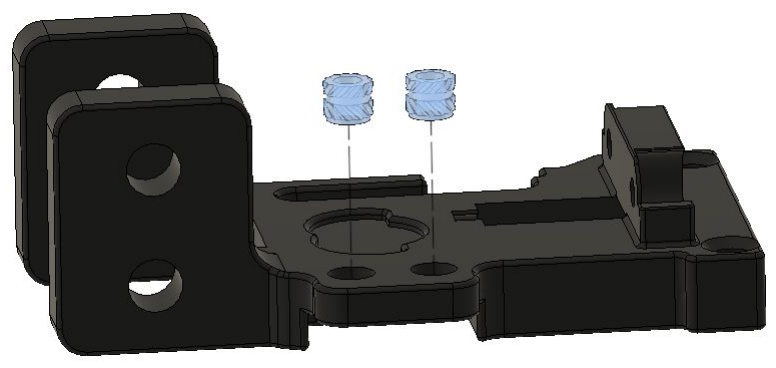
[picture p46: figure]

Preparation

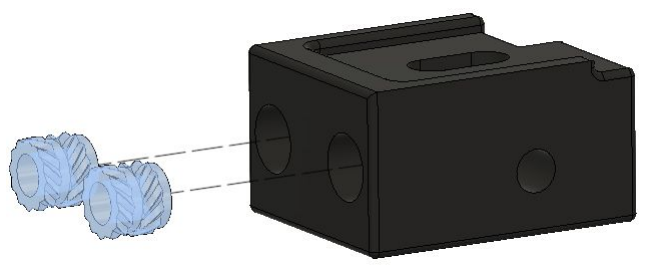
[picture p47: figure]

Insert the heat insert to the Spine Dock Body and Nozzle Blocker.

Preparation | https://github.com/Bikin-Creative/Lineux-Toolchanger

10 _______________________________________________________________________________________________________

Lineux was first developed on a Vzbot 330 printer.

_______________________________________________________________________________________________________ 11

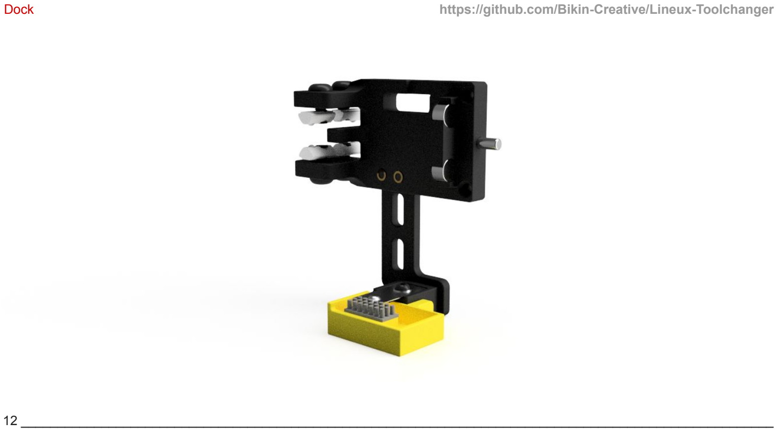
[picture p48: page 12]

Dock | https://github.com/Bikin-Creative/Lineux-Toolchanger

12 _______________________________________________________________________________________________________

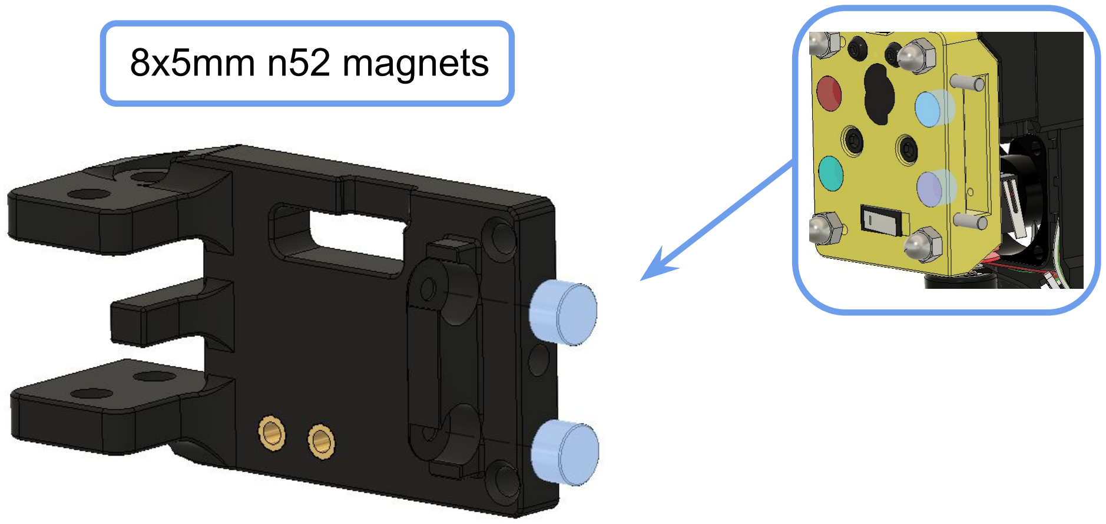
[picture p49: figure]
8x5mm n52 magnets

Apply a bit of glue/epoxy before inserting the magnets. Ensure the polarity matches the magnet on the Backplate that you install earlier. They should be attracted to each other when the toolhead is on the dock.

Dock

_______________________________________________________________________________________________________ 13

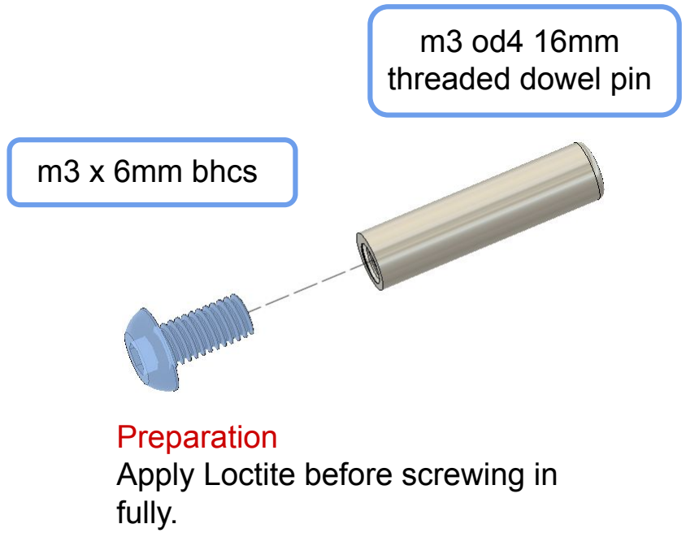
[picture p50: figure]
m3 od4 16mm threaded dowel pin; m3 x 6mm bhcs; Preparation Apply Loctite before screwing in fully.

Slide the dowel pin in the slot and push it all the way to the front.

Dock

14 _______________________________________________________________________________________________________

od6 id5 20mm spring

Slide the spring in the slot. Ensure the spring is seated properly on the buttonhead screw and the spring cutout.

Dock

_______________________________________________________________________________________________________ 15

Dock

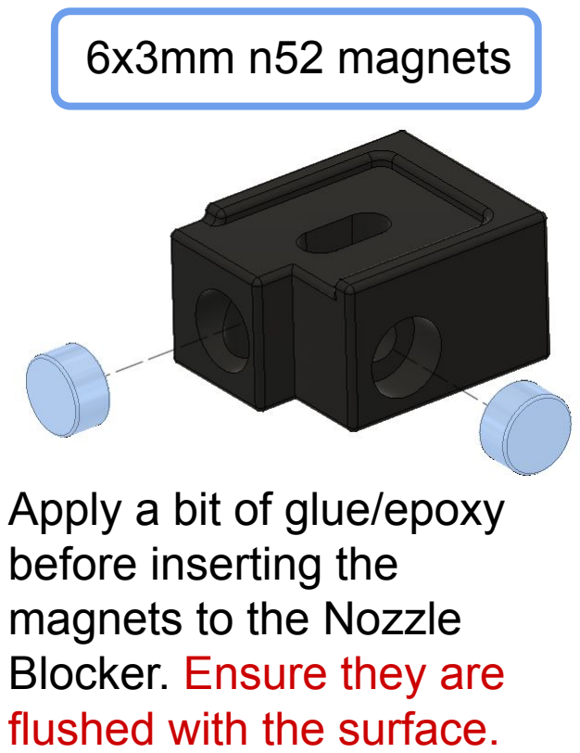
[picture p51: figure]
6x3mm n52 magnets; Apply a bit of glue/epoxy before inserting the magnets to the Nozzle Blocker. Ensure they are flushed with the surface.
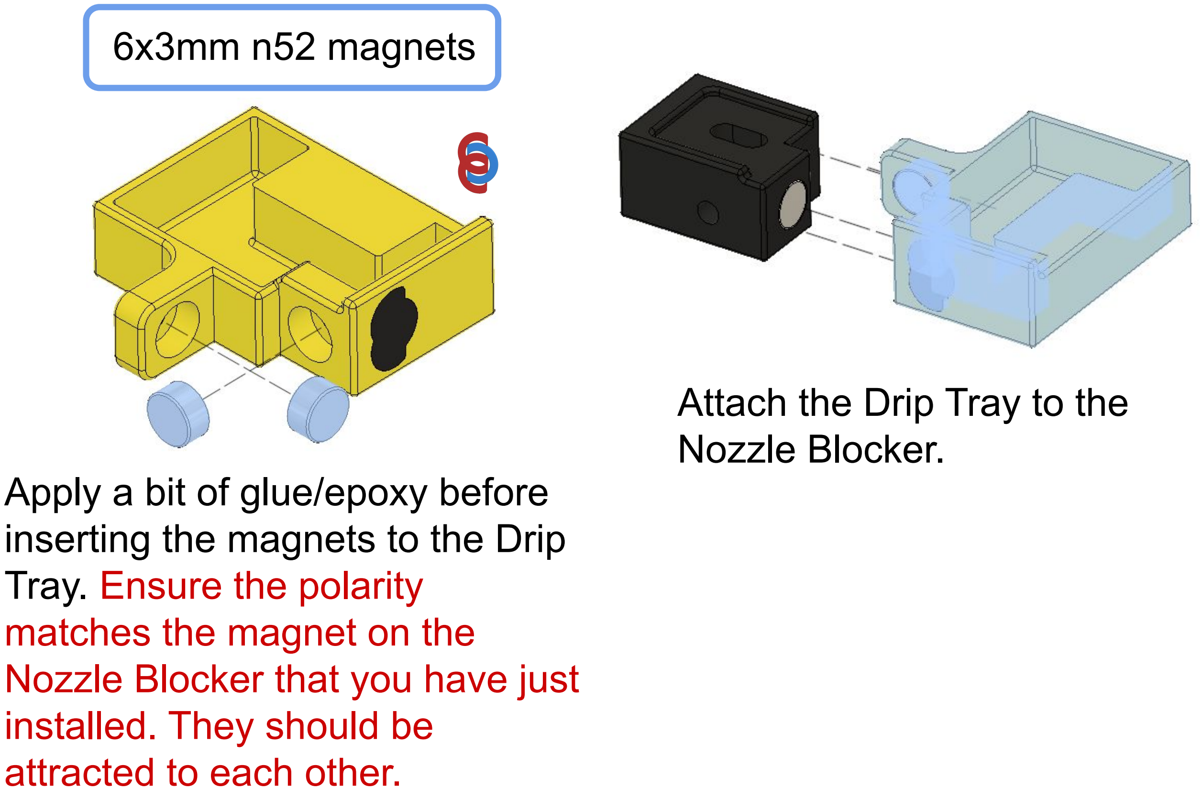
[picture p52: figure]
Apply a bit of glue/epoxy before inserting the magnets to the Drip Tray. Ensure the polarity matches the magnet on the Nozzle Blocker that you have just installed. They should be attracted to each other.; Attach the Drip Tray to the Nozzle Blocker.; 6x3mm n52 magnets

16 _______________________________________________________________________________________________________

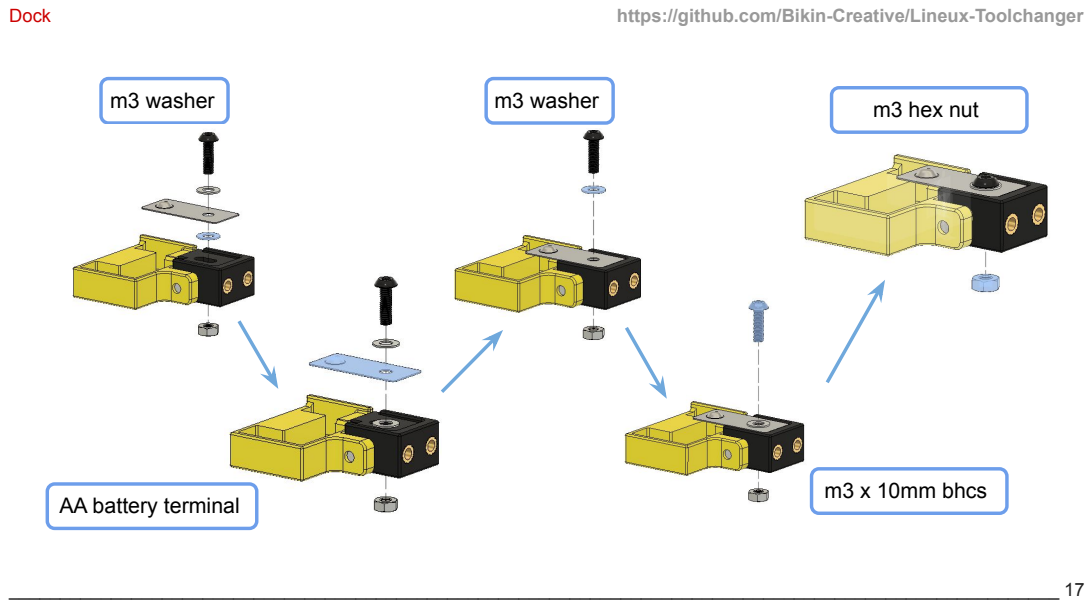
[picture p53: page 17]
m3 washer; AA battery terminal; m3 x 10mm bhcs; Dock

m3 hex nut m3 washer

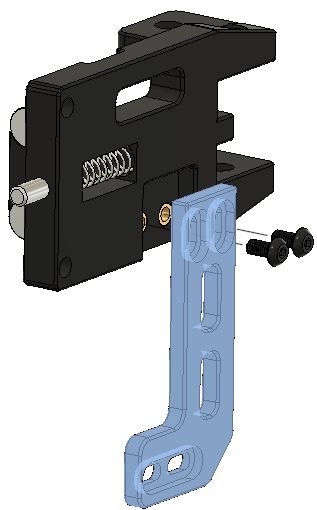
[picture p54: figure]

Attach the Nozzle Blocker Mount to the Dock.

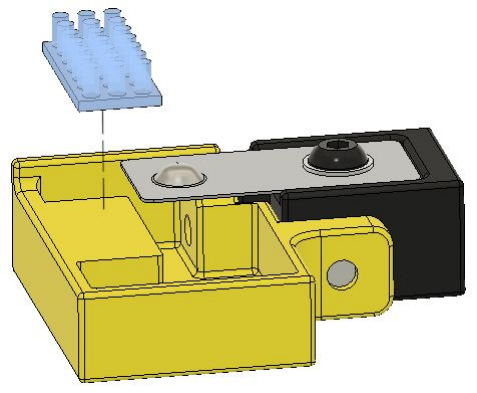
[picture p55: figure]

Attach the Silicone Brush.

Dock

18 _______________________________________________________________________________________________________

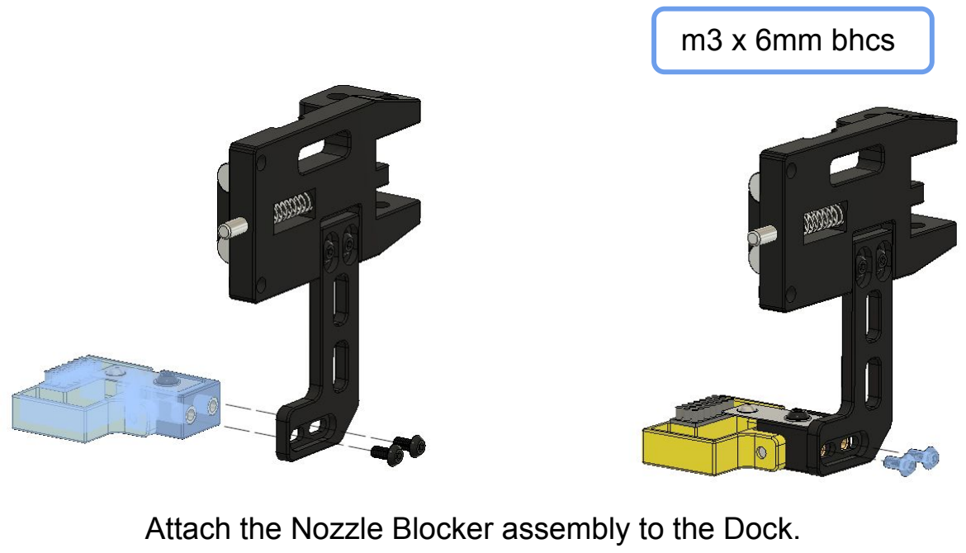
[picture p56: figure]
m3 x 6mm bhcs

Attach the Nozzle Blocker assembly to the Dock.

Dock

_______________________________________________________________________________________________________ 19

m5 t-nut

Slide in to both top and bottom of

the dock extrusion. | Slide in the complete Dock
| assembly to the dock extrusion.

Dock

20 _______________________________________________________________________________________________________

m5 x 12mm bhcs

Secure the Dock to the dock extrusion.

Dock

_______________________________________________________________________________________________________ 21

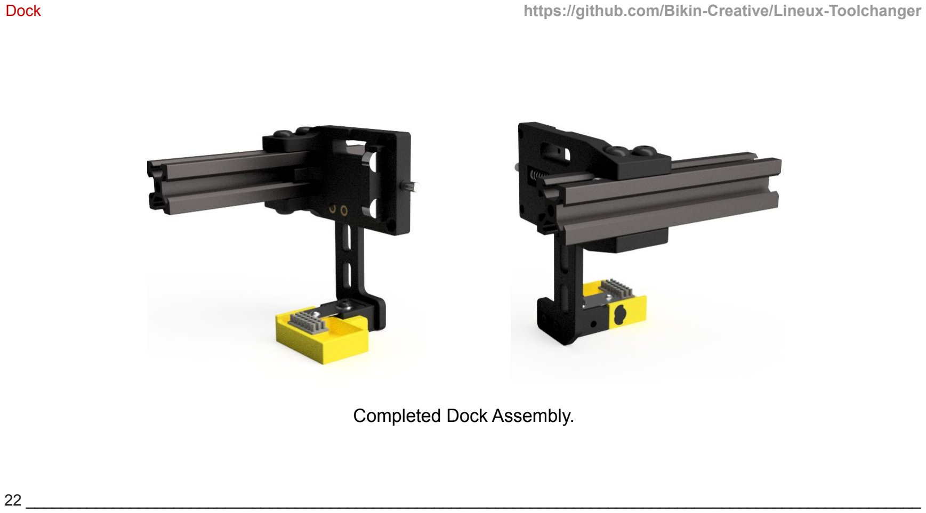
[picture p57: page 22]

Completed Dock Assembly.

Dock

22 _______________________________________________________________________________________________________

Lineux Ecosystem includes Lineux (Toolchanger), Dockslide (Movable Dock), BTC Klipper (Macros) and Tubby / Intai (Nozzle Offset Calibration Tool).

_______________________________________________________________________________________________________ 23

Spine Dock | https://github.com/Bikin-Creative/Lineux-Toolchanger

24 _______________________________________________________________________________________________________

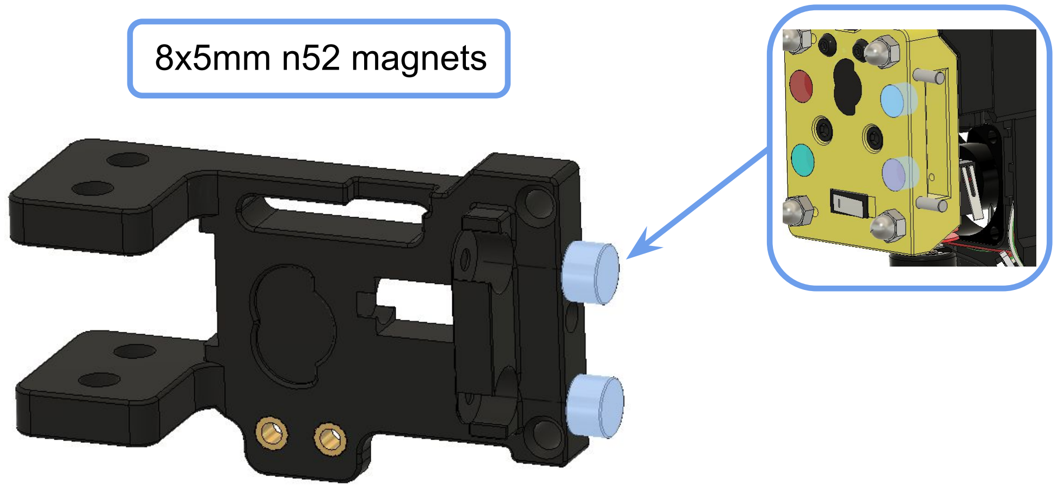
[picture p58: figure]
8x5mm n52 magnets

Apply a bit of glue/epoxy before inserting the magnets. Ensure the polarity matches the magnet on the Backplate that you install earlier. They should be attracted to each other when the toolhead is on the dock.

Spine Dock

_______________________________________________________________________________________________________ 25

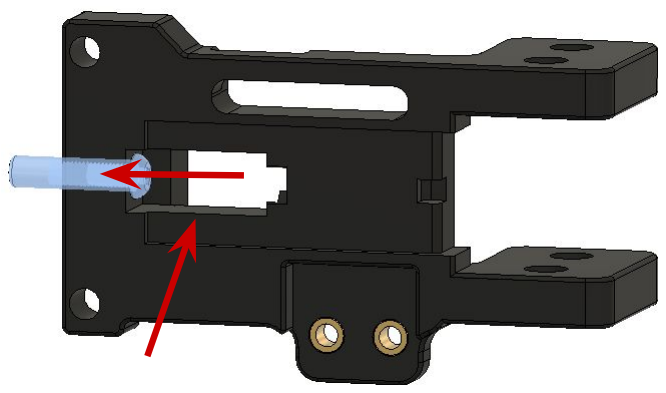
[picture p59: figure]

Slide the dowel pin in the slot and push it all the way to the front.

26 _______________________________________________________________________________________________________

Spine Dock

od6 id5 20mm spring

Slide the spring in the slot. Ensure the spring is seated properly on the buttonhead screw and the spring cutout.

_______________________________________________________________________________________________________ 27

Spine Dock

Spine Dock

28 _______________________________________________________________________________________________________

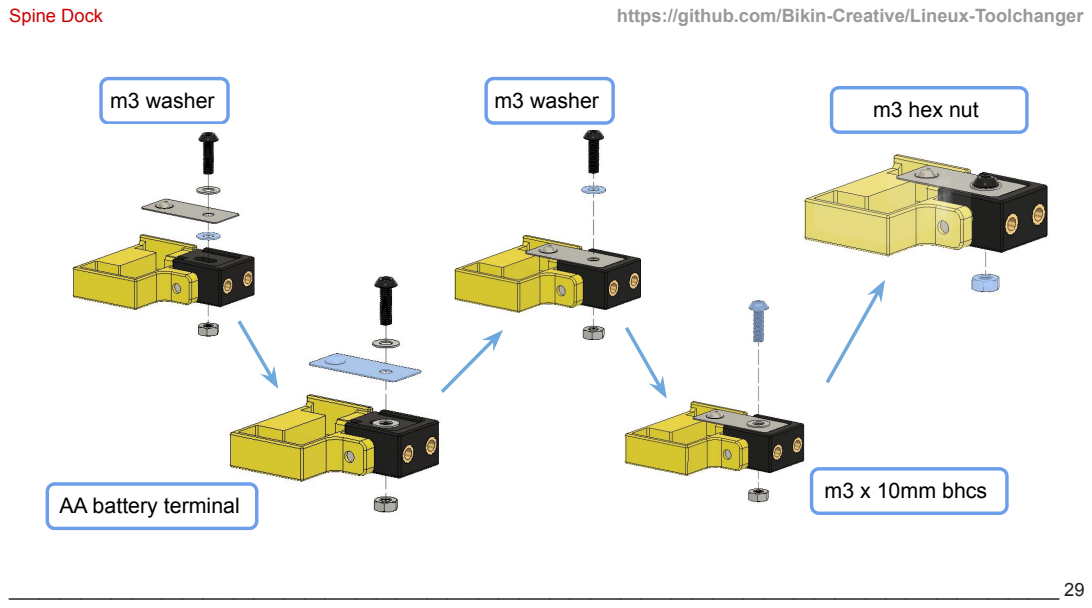
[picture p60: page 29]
m3 washer; AA battery terminal; m3 x 10mm bhcs; Spine Dock

m3 hex nut m3 washer

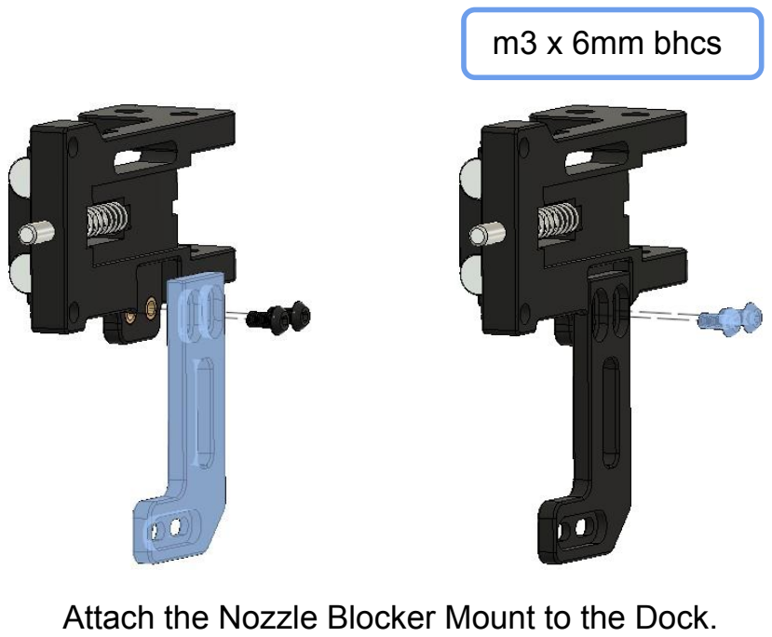
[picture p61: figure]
m3 x 6mm bhcs

Attach the Nozzle Blocker Mount to the Dock.

Attach the Silicone Brush.

Spine Dock

30 _______________________________________________________________________________________________________

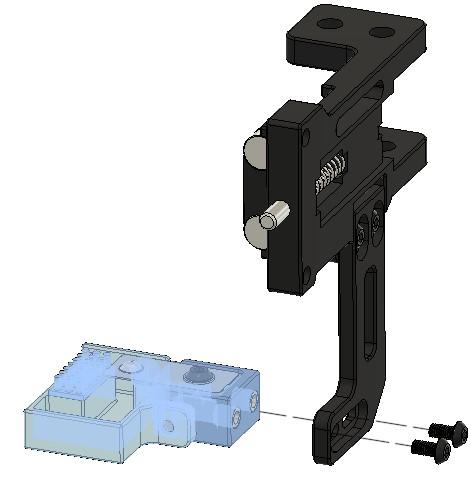
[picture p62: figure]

Attach the Nozzle Blocker assembly to the Dock.

Spine Dock

_______________________________________________________________________________________________________ 31

m5 t-nut

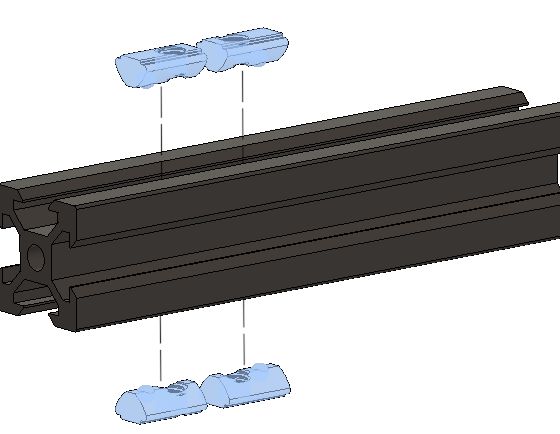
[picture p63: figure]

Slide in to both top and bottom of the dock extrusion.

Spine Dock

32 _______________________________________________________________________________________________________

Spine Dock | https://github.com/Bikin-Creative/Lineux-Toolchanger

_______________________________________________________________________________________________________ 33

m3 x 6mm fhcs

Attached the L-Bracket to the dock extrusion. You can keep it loose for now.

Spine Dock | https://github.com/Bikin-Creative/Lineux-Toolchanger

34 _______________________________________________________________________________________________________

Slide the Dock assembly on the inside of the L-Bracket onto the dock extrusion.

m5 x 12mm bhcs

Secure the Dock to the dock extrusion.

Spine Dock

_______________________________________________________________________________________________________ 35

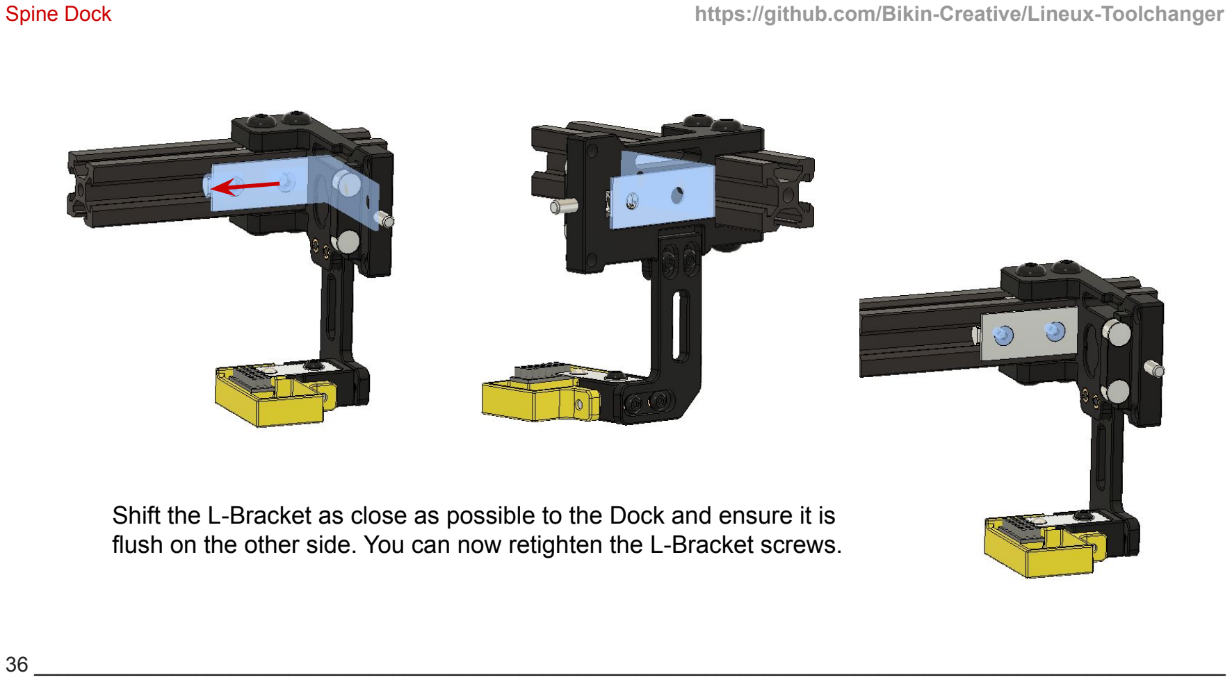
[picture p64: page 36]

Spine Dock | https://github.com/Bikin-Creative/Lineux-Toolchanger

36 _______________________________________________________________________________________________________

Shift the L-Bracket as close as possible to the Dock and ensure it is flush on the other side. You can now retighten the L-Bracket screws.

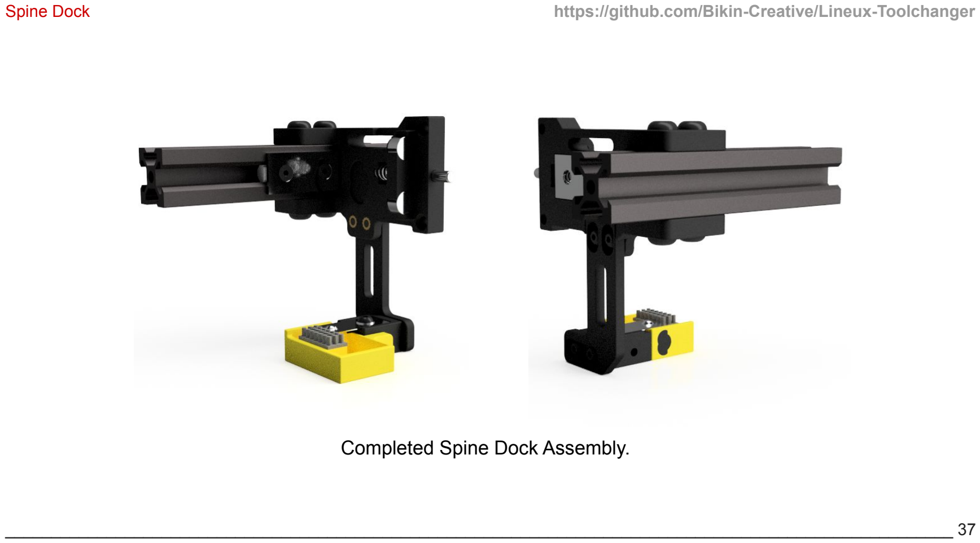
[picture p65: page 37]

Completed Spine Dock Assembly.

_______________________________________________________________________________________________________ 37

Spine Dock

38 _______________________________________________________________________________________________________

Completion | https://github.com/Bikin-Creative/Lineux-Toolchanger

We are humans and are prone to mistakes. If you encounter any issues/faults with the build guide, please raise them on our Discord with the relevant page number or a screenshot of the issues/fault.

This guide may be subjected to changes regularly based on feedbacks from the community.

_______________________________________________________________________________________________________ 23

Completion | https://github.com/Bikin-Creative/Lineux-Toolchanger

Do join us on Discord if you need help or have any questions.

https://discord.gg/Xwqbjj4VjH | https://github.com/Bikin-Creative/Lineux-Toolchanger

## Lineux Toolchanger

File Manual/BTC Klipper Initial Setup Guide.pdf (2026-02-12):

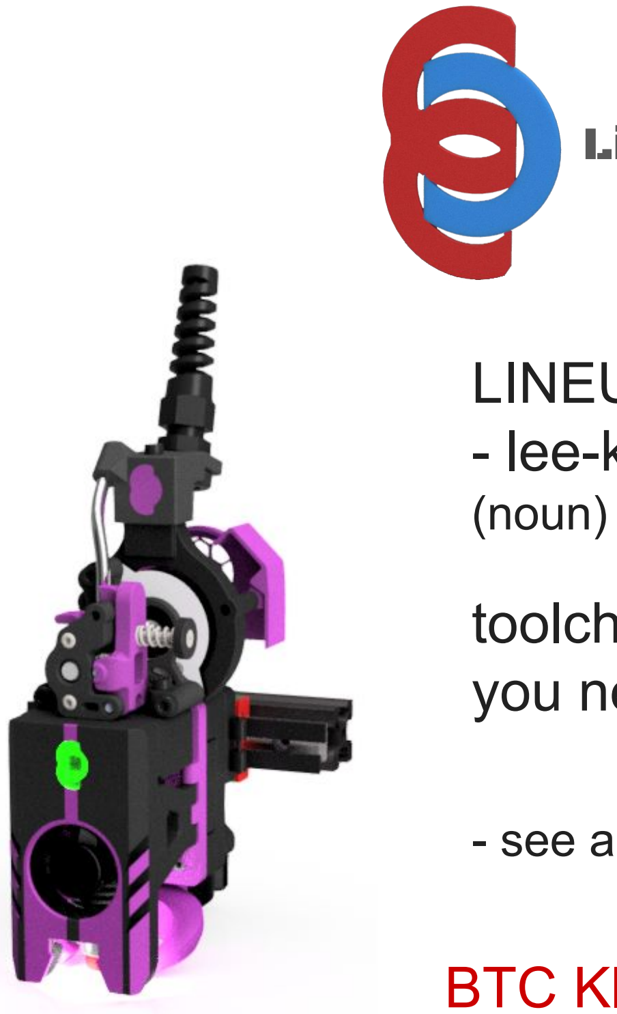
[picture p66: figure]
(noun)

## Lineux Toolchanger

## LINEUX - lee-knee-yurks

## toolchanger that print things you never know you need in a way you never imagine

- see also wizardry, mesmerizing

## BTC Klipper Initial Setup Guide

2025-02-11

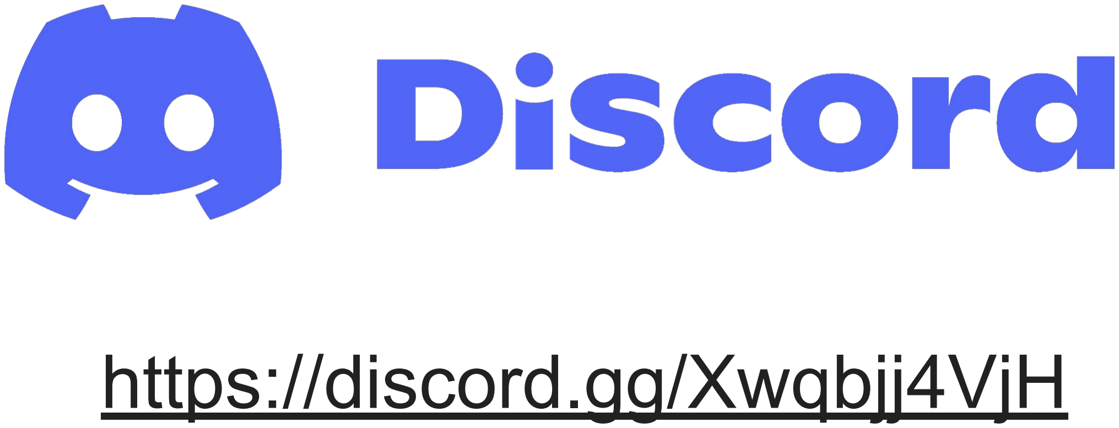
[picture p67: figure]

2 ________________________________________________________________________________________________________

https://discord.gg/Xwqbjj4VjH | https://github.com/Bikin-Creative/Lineux-Toolchanger

A big thank you to everyone who made this project possible.

## CAUTION

- Please take careful precautions with safety in mind when attempting to build Lineux.
- Only attempt the build if you are knowledgeable with 3d printer mechanics and electronics.
- Failure to follow safety precautions may result in things going against you, or even harm you.
- Magnets are extremely strong and may cause injuries. Please handle them with extra care.
- If things start to get confusing or you’re stuck at some point during the build, do ask questions on our discord.
- We try to keep things as simple and as clear as possible for a fun and enjoyable build for everyone.
- We are humans and are prone to mistakes. If you encounter any issues/faults with the build guide, please raise them on our Discord.

________________________________________________________________________________________________________ 3

Table Of Contents | https://github.com/Bikin-Creative/Lineux-Toolchanger

4 ________________________________________________________________________________________________________

Introduction | 05
Preparation | 06
BTC Variables Setup | 13
BTC Tool 0 Setup | 18
BTC Subsequent Tool Setup | 21
BTC Extras | 25
BTC Dockslide | 26
Toolboard Pin Assignment | 28

Introduction | https://github.com/Bikin-Creative/Lineux-Toolchanger

________________________________________________________________________________________________________ 5

Bikin Tool Changer (BTC) Klipper is a collection of Klipper macros created by @JackBeam that enables toolchanger functionality on any Klipper-based machine. It operates entirely through macros and does not require external plugins, making the system easier to understand, customize, and maintain.

Because BTC relies solely on native Klipper functionality, it is generally more resilient to Klipper updates and less likely to break. However, this approach also comes with some limitations in features and functionality, as it is constrained by what Klipper macros can support within the ecosystem.

This guide may be updated over time, so please check the Discord community if you have any questions or need the latest information.

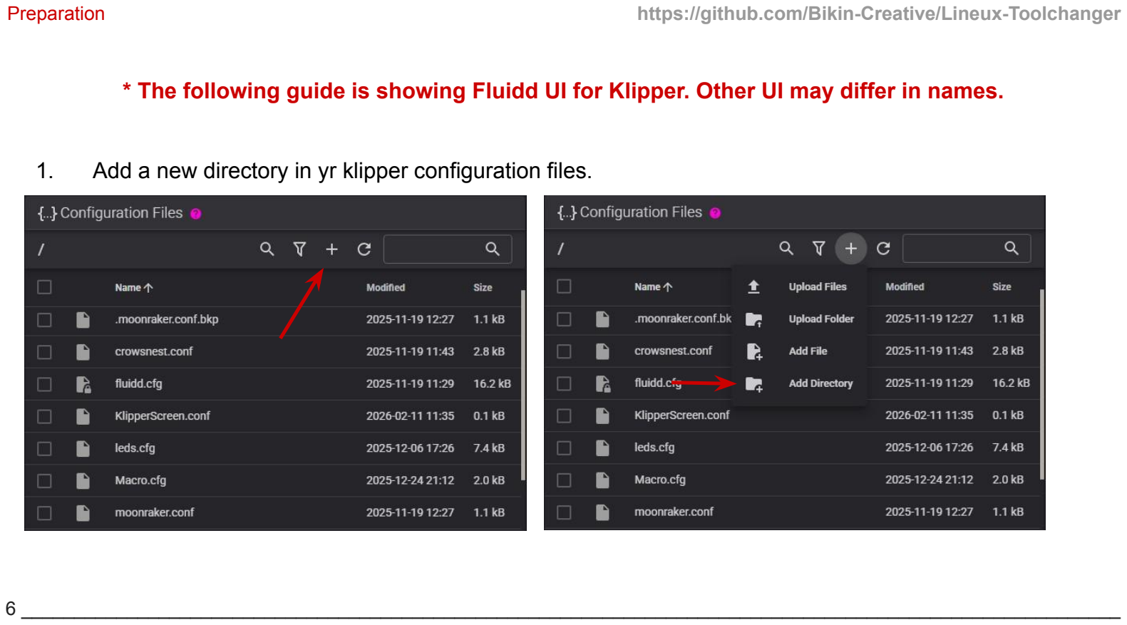
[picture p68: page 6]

Preparation | https://github.com/Bikin-Creative/Lineux-Toolchanger
1. Add a new directory in yr klipper configuration files.

* The following guide is showing Fluidd UI for Klipper. Other UI may differ in names.

6 ________________________________________________________________________________________________________

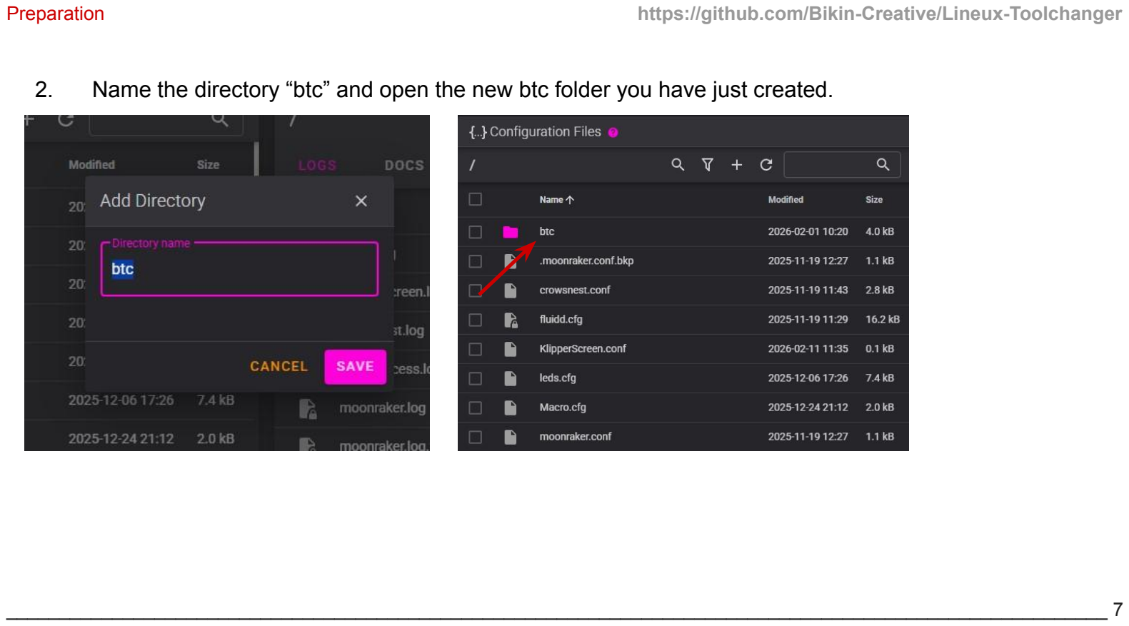
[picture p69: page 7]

Preparation | https://github.com/Bikin-Creative/Lineux-Toolchanger
2. Name the directory “btc” and open the new btc folder you have just created.

________________________________________________________________________________________________________ 7

Preparation | https://github.com/Bikin-Creative/Lineux-Toolchanger
3. Download all the config files from our github to your pc

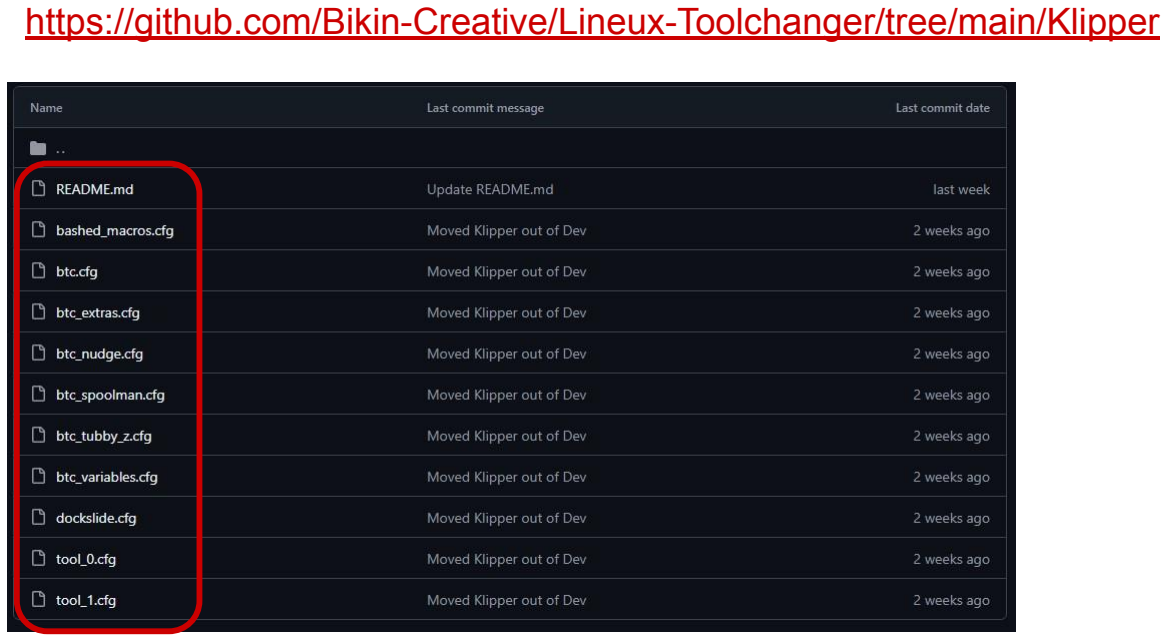
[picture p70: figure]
https://github.com/Bikin-Creative/Lineux-Toolchanger/tree/main/Klipper

8 ________________________________________________________________________________________________________

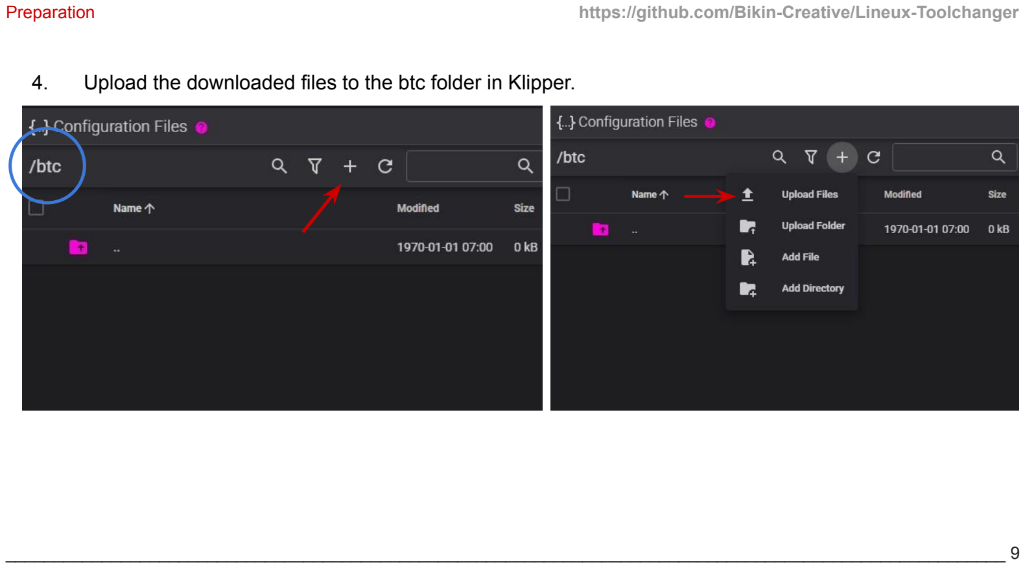
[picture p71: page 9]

Preparation | https://github.com/Bikin-Creative/Lineux-Toolchanger
4. Upload the downloaded files to the btc folder in Klipper.

________________________________________________________________________________________________________ 9

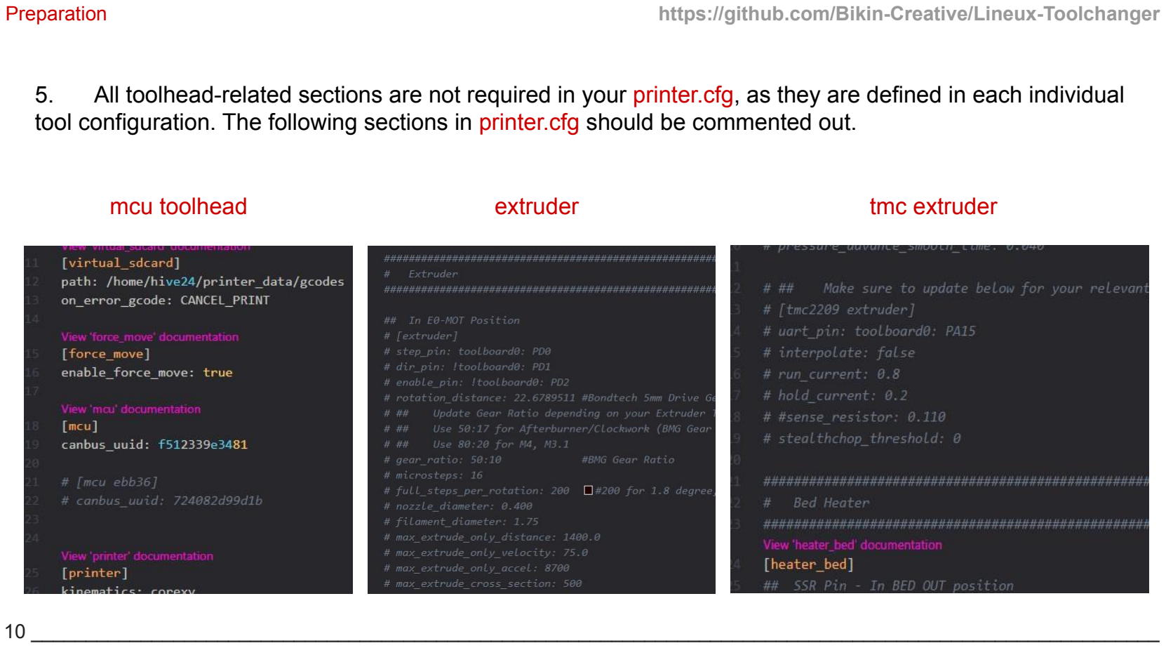
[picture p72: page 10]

Preparation | https://github.com/Bikin-Creative/Lineux-Toolchanger
5. All toolhead-related sections are not required in your printer.cfg, as they are defined in each individual tool configuration. The following sections in printer.cfg should be commented out.
mcu toolhead | extruder | tmc extruder

10 _______________________________________________________________________________________________________

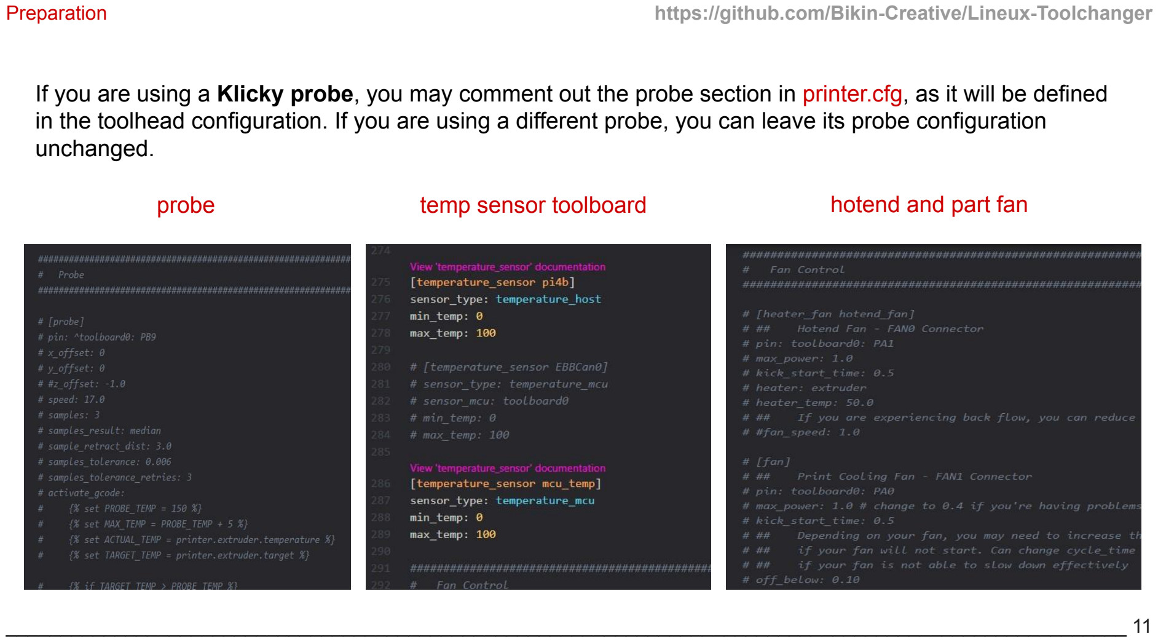
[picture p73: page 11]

Preparation | https://github.com/Bikin-Creative/Lineux-Toolchanger
probe | temp sensor toolboard | hotend and part fan

If you are using a Klicky probe, you may comment out the probe section in printer.cfg, as it will be defined
in the toolhead configuration. If you are using a different probe, you can leave its probe configuration unchanged.

_______________________________________________________________________________________________________ 11

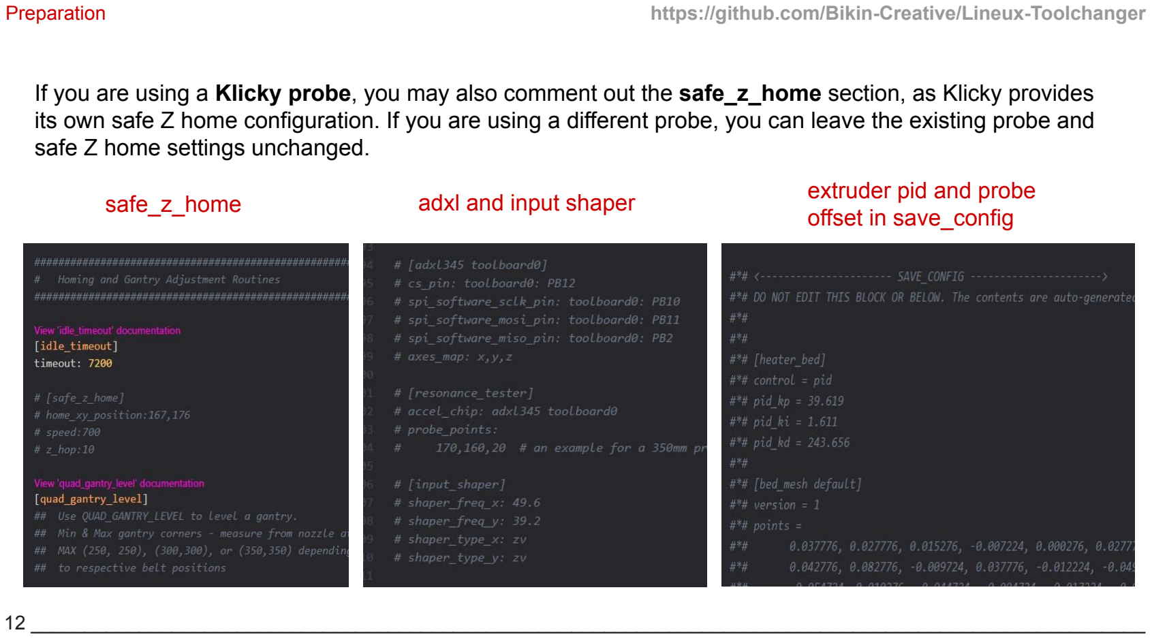
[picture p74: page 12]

Preparation | https://github.com/Bikin-Creative/Lineux-Toolchanger
safe_z_home | adxl and input shaper | extruder pid and probe offset in save_config

If you are using a Klicky probe, you may also comment out the safe_z_home section, as Klicky provides its own safe Z home configuration. If you are using a different probe, you can leave the existing probe and safe Z home settings unchanged.

12 _______________________________________________________________________________________________________

BTC Variables Setup | https://github.com/Bikin-Creative/Lineux-Toolchanger

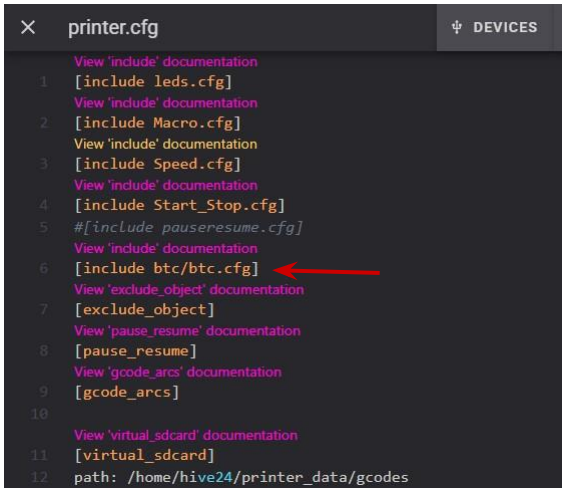
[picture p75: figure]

_______________________________________________________________________________________________________ 13

Include btc.cfg in your printer.cfg. Take note of the file path, as it is located in the btc folder.

BTC Setup | https://github.com/Bikin-Creative/Lineux-Toolchanger

Open btc_variables.cfg. By default, these three files are not commented out. You can leave them as they are for the initial setup.

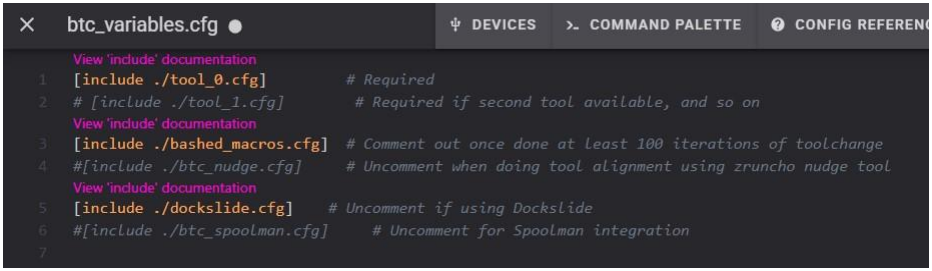
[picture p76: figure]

14 _______________________________________________________________________________________________________

BTC Setup | https://github.com/Bikin-Creative/Lineux-Toolchanger

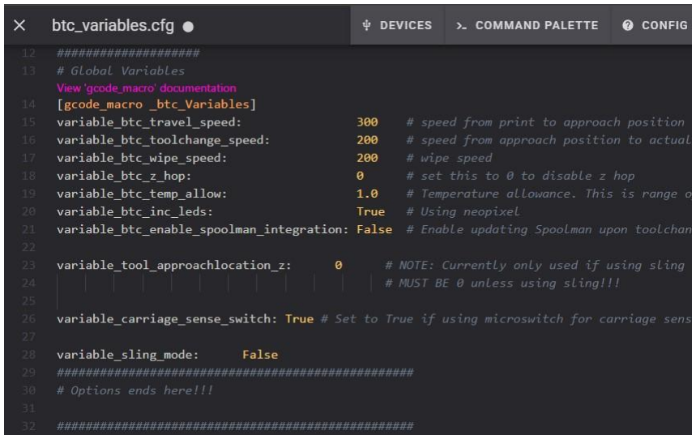
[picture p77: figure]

_______________________________________________________________________________________________________ 15

Under the global variables section, you may adjust the settings to suit your needs. For initial setup,
a slower speed of 100 is recommended.

BTC Setup | https://github.com/Bikin-Creative/Lineux-Toolchanger
a. variable_btc_travel_speed
Speed from print to approach location and from approach location back to print after tool pickup.
b. variable_toolchange_speed
Speed of toolchange sequence moves from approach location and back to approach location after a toolchange.
c. variable_btc_wipe_speed
Speed of tool wipe sequence.
d. variable_btc_z_hop
Z hop height during a toolchange. This is a separate z hop from the slicers z hop.
e. variable_btc_temp_allow
Hotend temperature allowance range. You may use a higher value if you find difficulty to get a stable set temperature after pid tuning.
f. variable_btc_inc_led
This is usually set to True unless you are not using leds on your tools.

16 _______________________________________________________________________________________________________

BTC Setup | https://github.com/Bikin-Creative/Lineux-Toolchanger

_______________________________________________________________________________________________________ 17 g. variable_btc_enable_spoolman_integration
Set to True if you are using Spoolman. This will enable updating Spoolman upon toolchanges. Some users have reported error when using this feature as its still a work in progress.
h. variable_tool_approachlocation_z
This must be set to 0 unless you are running BTC on Lineux Sling together with a dockslide.
i. variable_carriage_sense_switch
Currently this must be set to True since we are using a microswitch as the carriage sense. “carriage mounted probe as carriage sense” feature is still a work in progress.
j. variable_sling_mode
Set this to True only if you are running BTC on Lineux Sling. Else, it must be set to False.

https://github.com/Bikin-Creative/Lineux-Toolchanger

Each toolhead has its own configuration. Tool numbering starts from 0 instead of 1. For example:

- First tool = tool_0.cfg
- Second tool = tool_1.cfg
- Third tool = tool_2.cfg
- and so on.

BTC Tool_0 Setup


18 _______________________________________________________________________________________________________


https://github.com/Bikin-Creative/Lineux-Toolchanger

In tool_0.cfg, if you are using Klicky, set the carriagesense pin to use a pull-up (^). For Fysetc Tap, it can remain as a pull-down (~).

BTC Tool_0 Setup

_______________________________________________________________________________________________________ 19 https://github.com/Bikin-Creative/Lineux-Toolchanger

While some sections are already included and can remain at their default values, you will need to configure the following sections to match your specific setup.

1. [mcu toolboard0] (Set yr canbus uuid)
2. [extruder] (Set yr extruder settings)
3. [tmc2209 extruder] (Set yr tmc driver settings)
4. [probe] (Only for T0 using klicky which will be set as the master tool)
5. [resonance_tester] (Set yr probe points)

BTC Tool_0 Setup

20 _______________________________________________________________________________________________________

BTC Subsequent Tool Setup | https://github.com/Bikin-Creative/Lineux-Toolchanger

If you are using more than one tool, you must include each tool’s respective configuration in btc_variables.cfg. Ensure that section names and identifiers match the correct tool or toolboard numbers—for example: t1, t2, toolboard1, toolboard2, toolnumber=1, toolnumber=2, and so on.

BTC Subsequent Tool Setup; https://github.com/Bikin-Creative/Lineux-Toolchanger

BTC Subsequent Tool Setup; https://github.com/Bikin-Creative/Lineux-Toolchanger

BTC Subsequent Tool Setup; https://github.com/Bikin-Creative/Lineux-Toolchanger

_______________________________________________________________________________________________________ 25

BTC Extras | https://github.com/Bikin-Creative/Lineux-Toolchanger

BTC Extras contains sample macros that you can use to add or replace macros in your Klipper configuration. Sample macros include:

1. Print_Start
2. Print_End
3. Klicky homing_override
4. BED_MESH_CALIBRATE
5. QUAD_GANTRY_LEVEL
6. Z_TILT_ADJUST
7. Z_CALIBRATION_SET_OFFSET_MACRO

Since the probe is configured on Tool 0 (the master tool), sample macros are provided to ensure Tool 0 is automatically picked up whenever probing is required.

BTC Dockslide | https://github.com/Bikin-Creative/Lineux-Toolchanger

26 _______________________________________________________________________________________________________

Dockslide requires two stepper motors, each connected to its own stepper driver on the MCU. Two
endstop switches must also be connected to two endstop or signal ports on the MCU.

Lineux Sling, however, runs the Dockslide horizontally, allowing both motors to be driven from a single stepper driver port. When using this setup, ensure the stepper motor wiring is configured so that both motors move in the same direction when operating in parallel.

If you are using a stepper motor brake module with your Dockslide, you must connect the module to a 5V supply, a signal output, and ground.

BTC Dockslide | https://github.com/Bikin-Creative/Lineux-Toolchanger


_______________________________________________________________________________________________________ 27

The stepper brake module signal pin and the stepper_motor_right enable pin should be combined in the [multi_pin ds_brake] section. If you are not using a brake module, you can just rename the second pin to any unassigned pin on yr mcu.

The remaining stepper settings can be configured according to your stepper motor specifications.

Apply the same configuration approach to the left stepper motor as well.

Be sure to set the endstop pins for both motors.


Toolboard Pin Assignment | https://github.com/Bikin-Creative/Lineux-Toolchanger

28 _______________________________________________________________________________________________________


Toolboard Pin Assignment | https://github.com/Bikin-Creative/Lineux-Toolchanger

_______________________________________________________________________________________________________ 29


Toolboard Pin Assignment | https://github.com/Bikin-Creative/Lineux-Toolchanger

30 _______________________________________________________________________________________________________ https://github.com/Bikin-Creative/Lineux-Toolchanger

Your BTC initial setup is complete. Your next step will be to setup the toolchange configurations and calibrations. Do join us on Discord if you need help or have any questions.


https://discord.gg/Xwqbjj4VjH | https://github.com/Bikin-Creative/Lineux-Toolchanger

_______________________________________________________________________________________________________ 31 https://github.com/Bikin-Creative/Lineux-Toolchanger

We are humans and are prone to mistakes. If you encounter any issues/faults with the build guide, please raise them on our Discord with the relevant page number or a screenshot of the issues/fault.

This guide may be subjected to changes regularly based on feedbacks from the community.

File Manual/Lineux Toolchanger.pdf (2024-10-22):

## Lineux Toolchanger Build Guide

Originally Designed and Created by : 3dfiy My Life & JackBeam

With Contribution from :
Armon / art_v2.5091_sc0018

https://discord.gg/Xwqbjj4VjH https://github.com/Bikin-Creative/Lineux-Toolchanger

A big thank you to everyone who made this project possible.

Inspired by Axial Flux Toolchanger / Daksh Toolchanger Credit to chirpy2605 (Dragonburner Toolhead) (https://github.com/chirpy2605/voron)

1

# Important

- Pls take careful precautions with safety in mind when attempting to build Lineux.
- Only attempt the build if you are knowledgeable with 3d printer mechanics and electronics.
- Failure to follow safety precautions may result in things going against you, or even harm you.
- If things start to get confusing or you’re stuck at some point during the build, do ask questions on our discord. Learning is always a blessing.
- We try to keep things as simple and as clear as possible for a fun and enjoyable build for everyone.
- Accented Printed Parts has an (a) on the part description.
- Lineux Toolchanger utilises strong magnets. Magnets may interfere with fans therefore it's important to know the polarity of the magnets. If the polarity is unknown, you can use your phone compass to find the polarity of the magnets. Use a permanent marker to mark the North and South pole of the magnets. It makes it easier to keep track of the polarity
- The North pole of the magnets are marked Red in the illustration. The South pole of the magnets are marked Blue.
- We are humans and are prone to mistakes. If you encounter any issues/faults with the build guide, please raise them on our Discord.

Ready? Let’s go….

2

## Index

Carriage | 4
Toolhead | 16
Dock | 3

3

## Carriage

Lineux is adaptable to most printer. Illustration and build guide below shows the carriage assembly for the VZBot 330 Printer.


(Fun Facts : Lineux Toolchanger was first developed on the VzBot 330 Printer)

4

## Carriage

Printed Parts


Carriage Body Front x 1 | Carriage Body Top x 1


Carriage Body Bottom x 1 | Carriage Body Middle x 1


Carriage Body Rear x 1 | Locking Plate (a) x 1
Slider (a) x 1 | Belt Tensioner (a) x 2

5

## Carriage

Hardwares

1. m3x6mm shcs (3)
2. m3x8mm bhcs (1)
3. m3x8mm shcs (8)
4. m3x10mm shcs (4)
5. m3x12mm shcs (1)
6. m3x20mm shcs (1)
7. m3x30mm shcs (1)
8. m3x40mm bhcs (2)
9. m3 brass insert (13)
10. m3 hex nut (2)
11. m5 hex nut (3)
12. m3x16mm dowel pin (1)
13. m3x20mm dowel pin (2)
14. m3x35mm dowel pin (2)
15. m3x55mm dowel pin (2)
16. mr63zz bearing (4)
17. 10x5mm N52 magnet (6)

6

## Carriage

Insert 4 x m3 brass insert to the Carriage Body Top.


Assemble the Carriage Body Top to the MGN block using 4 x m3x10mm shcs. Pay attention to the orientation of the Carriage Body Top. Ensure the arrow on the Carriage Body Top is facing the front.

7


## Carriage

Insert 4 x m3 brass insert into the Carriage Body Bottom.


Install the Carriage Body Front and Carriage Body Bottom to the Carriage Assembly using 4 x m3x10mm shcs. Pay attention to the orientation of the Carriage Body Bottom. Ensure the arrow on the Carriage Body Bottom is facing the front.


8

## Carriage

Insert 3 x m3 brass insert into the Carriage Body Middle. Screw in m3x20mm shcs and m3x30mm shcs to the threaded hole from below. Do not overtighten because you are screwing into plastic. The m3x30mm shcs will go on the left side and the m3x20mm will go on the right side when viewed from the back as shown below. These 2 screws will provide strength support for the belt.


Install the Carriage Body Middle to the Carriage Assembly using 4 x m3x8mm shcs

9


## Carriage

Looks like you’re almost there towards completing the Carriage Assembly. Now is the perfect time to install the belts on the carriage. Insert m3 brass insert to both Belt Tensioner.


Run the rear belt in through the belt opening of the Carriage Body Middle and form a loop upon the belt exiting through the back. Slide the belt back in through the rear opening and pull on tight on the belt from the entrance point.This will ensure the belt is fitted snugly and locked in place.Repeat the same procedure for the opposite side.


Next, install the front belts. Ensure all belts are riding on the pulleys and idlers properly before committing to cutting the belts to length. Measure and cut the belt at 15mm from the edge of the Carriage Body Front.

10


## Carriage

Slide in the belt together with the Belt Tensioner in the Carriage Body Front. Screw in the m3x40mm bhcs from the opposite side to grab the Belt Tensioner but keep the belt a bit loose at this point. Once both Belt Tensioner are held in place, you can then adjust the belt tension as per yr printers recommended tension.


Congratulations, you have the base carriage installed. Your Carriage Assembly should look like this right now. Few more steps to go…

11


## Carriage

Insert 2 x m3 hex nuts, 1 in one of the magnet slot and 1 on the Locking Plate. Ensure the hex nuts are seated properly in the hex nut cutouts.


Install 6 x 10x5mm magnets on the Locking Plate. Pls ensure the correct orientation is followed. Refer to the colour image for the correct orientation. North is Red, South is Blue. Having the magnets installed in the wrong orientation may affect the Part Cooling Fans and stop them from working. The magnets should be a tight fit in the slots. It’s recommended to apply a few drops of glue in the slots before pushing the magnets in. A wooden mallet might also be handy to ensure the magnets are seated fully in and properly.


Install the m3x16mm dowel pin on the Locking Plate arm.

12

## Carriage

Slide in 4 x mr63zz bearings in the respective slots on the Slider and push in the 2 x m3x20mm dowel pins to hold the bearings in place.


Next, prepare the Carriage Body Rear. Insert 2 x m3x35mm dowel pins in the 2 slots and push in the 2 x m3x55mm dowel pins from the top. Ensure the dowel pins sit flush with the Carriage Body Rear at the top.

13


## Carriage

Place the assembled Locking Plate magnets side face down on a flat surface and place the Carriage Body Rear on top. Place the assembled Slider on top of the Locking Plate and screw them down using m3x8mm bhcs and m3x12mm bhcs. The m3x8mm should be on the right (closer to Locking Plate Arm) and the m3x12mm on the left when viewed from the front. It is advisable to apply threadlocker to the 2 screws to prevent them getting loose. After completed, slide the Locking Plate back and forth. They should move freely without any resistance.


It's time to complete the whole Carriage Assembly. Install the Carriage Body Rear to the Carriage Assembly and screw it down using 3 x m3x6mm shcs. You can then push in 3 x m5 hex nuts on top of the screws. The m5 hex nuts should be a push tight fit to prevent them from accidentally dropping out.

14


## Carriage

Congrats on completing the Carriage Section. Job well done. Remember to take breaks in between assemblies. Your final Carriage Assembly should look like this.


## Checklist

- Ensure the Locking Plate can move freely without resistance.
- Try to move the carriage around. Ensure the m5 hex nuts stay in place.
- Ensure you have the proper belt tension.
- Ensure all screws are tightened.

Let’s assemble the Toolhead next once you’re ready to rock and roll…

15

## To Be Continued…

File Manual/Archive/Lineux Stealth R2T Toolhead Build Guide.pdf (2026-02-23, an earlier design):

## Lineux Toolchanger

## LINEUX - lee-knee-yurks

## toolchanger that print things you never know you need in a way you never imagine

### - see also wizardry, mesmerizing

## Lineux Stealth R2T Build Guide

2025-02-06

2 ________________________________________________________________________________________________________

https://discord.gg/Xwqbjj4VjH | https://github.com/Bikin-Creative/Lineux-Toolchanger

## A big thank you to everyone who

made this project possible.

________________________________________________________________________________________________________ 3

## CAUTION

- Please take careful precautions with safety in mind when attempting to build Lineux.
- Only attempt the build if you are knowledgeable with 3d printer mechanics and electronics.
- Failure to follow safety precautions may result in things going against you, or even harm you.
- Magnets are extremely strong and may cause injuries. Please handle them with extra care.
- If things start to get confusing or you’re stuck at some point during the build, do ask questions on our discord.
- We try to keep things as simple and as clear as possible for a fun and enjoyable build for everyone.
- We are humans and are prone to mistakes. If you encounter any issues/faults with the build guide, please raise them on our Discord.

Table Of Contents | https://github.com/Bikin-Creative/Lineux-Toolchanger

4 ________________________________________________________________________________________________________

Introduction | 05
Hardware | 07
Preparation | 09
Toolhead | 12
LED Assist Tool | 45
Toolboard Wiring | 50
Completion | 53

Introduction | https://github.com/Bikin-Creative/Lineux-Toolchanger

________________________________________________________________________________________________________ 5

Part Printing Recommendations Recommended setting/material to print your parts.

Material
ABS

Layer Height
0.2mm

Extrusion Width
0.4mm

Infill
40% ( Grid, Gyroid, Honeycomb, Triangle, Cubic )

Number of Walls
4

Number of Top/Bottom
5

https://github.com/Bikin-Creative/Lineux-Toolchanger

6 ________________________________________________________________________________________________________

Introduction

Parts Filename Guide

Primary Colour

Eg. carriage_A.stl

These are to be printed
with your primary/base
colour.

Accent Colour

Eg. [a]_locking_plate.stl

Files with [a] in front are to be printed with your
secondary/accent colour.
Parts will be indicated
with the Lineux Logo
beside it in this guide.

Quantity Required

Eg. belt_tensioner_x2.stl

Files ending with x#
indicate the quantity
required to be printed

To make your build easier, we recommend you to download the cad from our github to enable you to visualize the whole assembly.

Hardware | https://github.com/Bikin-Creative/Lineux-Toolchanger

________________________________________________________________________________________________________ 7

Button Head Cap Screw
(BHCS)

Heat Insert

Dowel Pin

Socket Head Cap Screw
(SHCS)

n52 Magnet

Hex Nut

Ring Terminal

Set Screw / Grub Screw

Cap Nut / Dome Nut

Lineux was first developed on a Vzbot 330 printer.

8 ________________________________________________________________________________________________________

Preparation | https://github.com/Bikin-Creative/Lineux-Toolchanger

It is recommended to install all heat inserts first on all the parts prior to starting the build. The build guide is for R2T setup with Revo Voron, Sherpa Micro, EBB36 and Klicky.

Toolhead; m3 heat insert; m4 heat insert; Preparation; respective slots as shown.; Preparation Insert the heat inserts to the Cowl Klicky.

Insert the heat insert to the Backplate in the

Preparation | https://github.com/Bikin-Creative/Lineux-Toolchanger

Toolhead

m3 heat insert

Preparation
Insert the heat inserts to the Revo Voron Plate.


Preparation
Insert the heat inserts to the Sherpa Micro Ebb Mount.

10 _______________________________________________________________________________________________________

Lineux originally started with a modified Dragonburner toolhead, but has since transitioned to using its own Lineux One toolhead.

_______________________________________________________________________________________________________ 11

Toolhead | https://github.com/Bikin-Creative/Lineux-Toolchanger

12 _______________________________________________________________________________________________________

Magnet Mounting Tool

Magnet Polarity
Configuration

Place the Backplate on
the Magnet Mounting
Tool. This will make
installing the magnets
easier.

8x5mm n52 magnets

Insert the magnets in the respective slots. Apply a bit of epoxy or glue before inserting the magnets. You may use a mallet or a wrench to push the magnets in and ensure they are flushed with the top surface. Take note of the magnet polarity configuration. Ensure they are the opposite polarity to the configuration on your Locking Plate. This will enable the respective magnets to attract when the Toolhead is engaged to the Carriage.

_______________________________________________________________________________________________________ 13

Preparation
Screw in the set screw to the cap nuts. Apply loctite before screwing.


Apply just a bit of Loctite on the set screw thread close to the cap nut before installing. The set screw will screw through the heat insert and into plastic. Be careful not to allow the Loctite to touch any printed part of the Backplate as it will degrade the material.

14 _______________________________________________________________________________________________________

Black; RED; Green

* This step is only applicable if you are running Lineux on Fysetc CNC Tap

Before inserting the m4 cap nuts, stripped 3 wires and
insert them into the indicated holes. Ensure the
stripped ends are below the m4 cap nuts location.
Take note of the wire polarity.

16 _______________________________________________________________________________________________________

Screw in the cap nuts while ensuring it pinch against the stripped ends of the wires. Use a multimeter to check for continuity.

Carriage Sense; Preparation Solder 2 wires to the 90deg micro switch. Take note to solder the wires to C and NC pin on the micro switch. Different supplier may have different pin array.

Thread the wire into the cutout slot and rotate the switch as you push it in. It should sit all the way in the slot.

_______________________________________________________________________________________________________ 17

Dock Sense

Strip the end of 2 wires and
thread them into the wire slot.
Ensure the stripped ends exit
into the dowel slots.

Apply a bit of glue before inserting the dowel pins. Ensure the dowel pins are resting and pushed against the stripped end of the 2 individual wires. Use a multimeter to check for continuity.

_______________________________________________________________________________________________________ 19


Remove the 2 cutaway support included in the Backplate during printing.

20 _______________________________________________________________________________________________________

m3 x 8mm bhcs

_______________________________________________________________________________________________________ 21

Part Cooling Fan Connector; Slide the ring terminals on the bolt. Ensure the wires colours matched the spring wires on the carriage that you installed earlier as these will determine voltage and ground for the part cooling fan.; Secure the ring terminals.; m3 hex nut

6x3mm n52 magnets


Apply glue before pushing in the magnet. Ensure they sit flushed in the slot.

_______________________________________________________________________________________________________ 23


Completed Backplate assembly.

24 _______________________________________________________________________________________________________

Slot in the 3010 fan into

how to use the Led Assist Tool.); status led; nozzle led; to toolboard

position. | Preparation
| Wire the neopixel leds in this array. The first led from the toolboard will be the
| status led and the next 2 are the nozzle
| leds. (Refer to page 45 for the guide on

Slot in the Led
Diffuser.

_______________________________________________________________________________________________________ 25

Insert the leds into position in their respective slots.

You can tuck in any excess wire in

the wire channel.

26 _______________________________________________________________________________________________________


Route the fan and led wires along the side arm of the Cowl. You will cable tie the wires together later.

Cover the status led with the Led Stopper.

_______________________________________________________________________________________________________ 27

6x3mm n52 magnets; Apply a bit of glue/epoxy before inserting the magnets. Take note of the indicated magnet. Ensure the polarity matches the magnet on the Backplate that you install earlier. They should be attracted to each other.

* This step is for Klicky Probe. You may skip this if you are not using Klicky Probe.


You can now cable tie the led wires, fan wires and klicky wires together on the cowl arm.

Completed Cowl Assembly

30 _______________________________________________________________________________________________________

* This guide is showing the Revo Voron hotend. Other hotends may require different printed parts, hardware or steps.

_______________________________________________________________________________________________________ 31

Attached the Revo Voron hotend.

m3 x 8mm shcs

Ptfe tube 47mm

Slide the Ptfe tube fully in.

32 _______________________________________________________________________________________________________

* This guide is showing the Sherpa Micro Extruder. Other extruders may require different printed parts, hardware or steps.

m3 x 12mm shcs; Secure the Sherpa Micro Extruder to the assembly.

_______________________________________________________________________________________________________ 33

filament 37mm; Rotate the Cowl assembly 90° and align the swivel hinge with the Backplate; both assemblies together. You can pinch; secure it in place.

assembly. Slide in the filament to secure

both ends of the filament using a plier to

34 _______________________________________________________________________________________________________

Route all the wires from the Cowl into the middle channel of the Backplate as shown. Keep the Cowl in the 90° position.

_______________________________________________________________________________________________________ 35


Position the hotend assembly closer to the Backplate and route the hotend and thermistor wires through the middle of the Backplate and upwards similar to the rest of the wires.

Once all wires are in position, you can slide down the Cable Helper to secure the wires in place.

36 _______________________________________________________________________________________________________


Close the Cowl. It should stay securely in place via the magnets.

m3 x 10mm bhcs

m3 x 25mm shcs

Secure the hotend/extruder assembly to the Backplate.

_______________________________________________________________________________________________________ 37

38 ______________________________________________________________________________________________________

Replace the 3 bolts of Sherpa Micro extruder to the replacement size of screws shown.


_______________________________________________________________________________________________________ 39

* This guide is showing the Bigtreetech Ebb36 toolboard. Other toolboards may require different printed parts, hardware or steps.

m3 hex nut

Attach the Sherpa Micro Ebb Mount to the extruder and secure them with the hex nuts.

40 ______________________________________________________________________________________________________

Temporary attach the Ebb36 to the Ebb36 mount.

m3 x 35mm shcs

Toolboard Spacer

toolboard wiring diagram (page 107) for reference.

_______________________________________________________________________________________________________ 41

Route all the wires from the Backplate and connect them to their respective connectors/pins on the toolboard. Trim the wires as required and crimp their appropriate connector. Refer to the

42 ______________________________________________________________________________________________________

Remove the 2 bolts and attach the Toolboard Cover after you have connected all the wires.

Secure the Umbilical Adapter to the Ebb36 Mount.; m3 x 10mm shcs

_______________________________________________________________________________________________________ 43

Attach the PG7 Flex Gland
to the Umbilical Adapter.

44 ______________________________________________________________________________________________________

Completed Toolhead Assembly

Led Assist Tool | https://github.com/Bikin-Creative/Lineux-Toolchanger

_______________________________________________________________________________________________________ 45

Place 2 leds into A and B slot as shown on the Led Soldering Jig. Pay attention to the orientation of the direction on the Leds.

Led Assist Tool | https://github.com/Bikin-Creative/Lineux-Toolchanger

46 ______________________________________________________________________________________________________

Solder 3 wires as shown. The wiring should be from DOUT of A to DIN of B.

Led Assist Tool | https://github.com/Bikin-Creative/Lineux-Toolchanger

_______________________________________________________________________________________________________ 47

Place the next Led into the C slot as shown. Pay attention to the orientation of the direction on the Led.

Led Assist Tool | https://github.com/Bikin-Creative/Lineux-Toolchanger

48 ______________________________________________________________________________________________________

Solder 3 wires as shown. The wiring should be from DIN of A to DOUT of C. Pay attention to the polarity of the wires. Ensure 5v, data and ground are soldered accordingly.

Led Assist Tool | https://github.com/Bikin-Creative/Lineux-Toolchanger

_______________________________________________________________________________________________________ 49

Finally, solder three wires (approximately 150 mm long) to the DIN of the LED in slot C. You may choose to make the wires slightly longer to provide extra slack and avoid issues if the wires are too short.


Toolboard Wiring | https://github.com/Bikin-Creative/Lineux-Toolchanger

50 ______________________________________________________________________________________________________

Toolboard Wiring | https://github.com/Bikin-Creative/Lineux-Toolchanger

_______________________________________________________________________________________________________ 51


Toolboard Wiring | https://github.com/Bikin-Creative/Lineux-Toolchanger

52 ______________________________________________________________________________________________________

Completion | https://github.com/Bikin-Creative/Lineux-Toolchanger

We are humans and are prone to mistakes. If you encounter any issues/faults with the build guide, please raise them on our Discord with the relevant page number or a screenshot of the issues/fault.

This guide may be subjected to changes regularly based on feedbacks from the community.

_______________________________________________________________________________________________________ 53

Completion | https://github.com/Bikin-Creative/Lineux-Toolchanger

Do join us on Discord if you need help or have any questions.

https://discord.gg/Xwqbjj4VjH | https://github.com/Bikin-Creative/Lineux-Toolchanger

54 ______________________________________________________________________________________________________

## Lineux Toolchanger

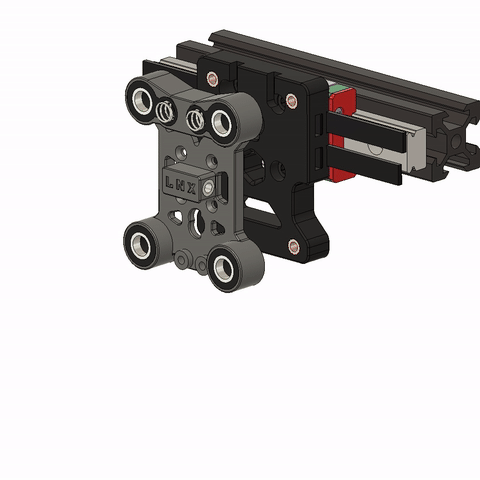
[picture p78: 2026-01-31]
Images/lineux_stealthc_voron_printed_carriage.gif

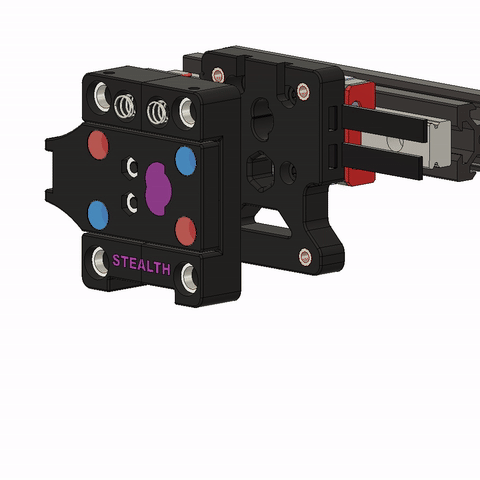
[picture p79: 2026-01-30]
Images/voron_printed_carriage.gif

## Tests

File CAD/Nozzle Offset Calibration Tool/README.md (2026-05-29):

# Overview

Tubby and Intai are nozzle offset calibration tool designed with minimal hardware and simplicity in mind. Several variations of Tubby and Intai are available, allowing you to choose the version that best suits your requirements.

If the magnet used is not strong enough to securely hold the floating version of Tubby or Intai on the print bed, you may opt for the larger magnet base for improved stability.

Bom for both Tubby and Intai is [Here](https://github.com/Bikin-Creative/Lineux-Toolchanger/tree/main/BOM)

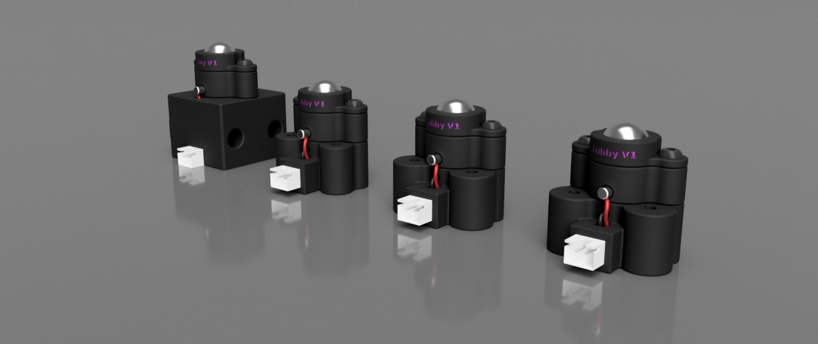
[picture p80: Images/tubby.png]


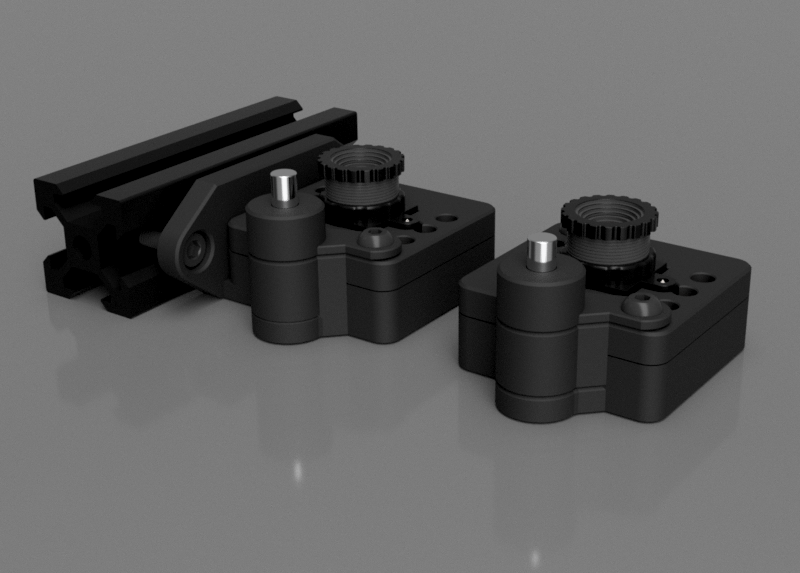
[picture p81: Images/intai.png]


# Tubby Deviation Sample
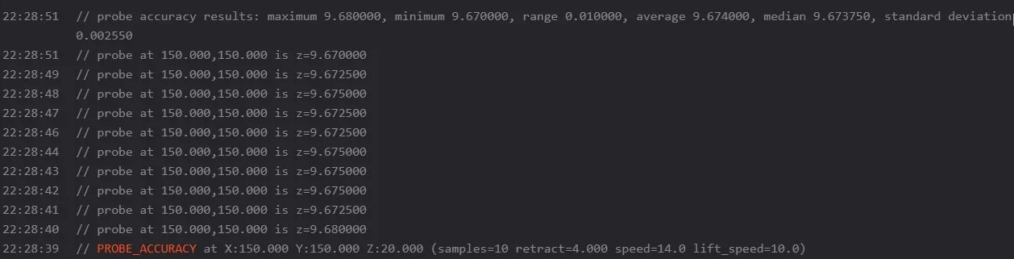
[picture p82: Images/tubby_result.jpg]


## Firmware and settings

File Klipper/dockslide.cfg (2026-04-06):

[gcode_macro _dockslide_variables]
variable_travel_speed: 100      # Dockslide travel speed.You may set higher if your motor doesnt skipped steps
variable_deploy_height: 10      # Height at which the dockslide extrusion is level with the gantry extrusion
variable_deploy_offset: 0       # Set to 0 for fixed gantry
variable_park_height: 100       # Height at which the parked tools cleared the tool on the carriage
variable_safe_y: 100            # Y coordinate at which the dockslide can deploy without hitting the tool on the carriage
variable_safe_z: 20             # Z height at which the dockslide can deploy the parked tools without hitting the bed
variable_front_dock: True       # Set to False if you have the tools parked at the rear
variable_travel_resolution: 1   # You may leave it as is
######################################
# Below variables are used during runtime. DO NOT edit!!
variable_dockslide_status: 0 # 0: unknown, 1: park, 2: deploy: 3:standby
variable_dockslide_homed: False
variable_doing_homing: False
variable_travel_acc: 5000
variable_home_init_speed: 30
variable_home_init_move: 5
variable_cur_pos_right: 5
variable_cur_pos_left: 5
variable_count: 0
variable_count1: 0
variable_motornum: 2
variable_flying_gantry: False
gcode:

[multi_pin ds_brake]
pins: !PE2, PA0

[tmc2209 manual_stepper motor_right]
uart_pin: PB7
run_current: 1.0
hold_current: 0.5
interpolate: False
stealthchop_threshold: 0

[manual_stepper motor_right]
step_pin: PE1
dir_pin: PE0
enable_pin: multi_pin:ds_brake
full_steps_per_rotation: 200
rotation_distance: 40
microsteps: 16

[gcode_button dockslide_endstop_right]
pin: ^PB12
press_gcode:
release_gcode:

#################################################
# Second motor for vertical Dockslide
# Horizontal Dockslide does not require second motor since both motors combined into a single stepper driver
# For horizontal Dockslide, eg in sling, Comment out the following
[tmc2209 manual_stepper motor_left]
uart_pin: PB3
run_current: 1.0
hold_current: 0.5
interpolate: False
stealthchop_threshold: 0

[manual_stepper motor_left]
step_pin: PB5
dir_pin: !PB4
enable_pin: !PB6
full_steps_per_rotation: 200
rotation_distance: 40
microsteps: 16

[gcode_button dockslide_endstop_left]
pin: ^PB13
press_gcode:
release_gcode:
# Second motor ends
#####################################################

[gcode_macro Dockslide_Check_Status]
gcode:
  {% set dockslide_status = printer["gcode_macro _dockslide_variables"].dockslide_status %}
  {% if dockslide_status == 0 %}
    {% set statustxt = "Unknown" %}
  {% elif dockslide_status == 1 %}
    {% set statustxt = "Park" %}
  {% elif dockslide_status == 2 %}
    {% set statustxt = "Deploy" %}
  {% else %}
    {% set statustxt = "Standby" %}
  {% endif %}
  { action_respond_info("Dockslide: " + statustxt) }

[gcode_macro Dockslide_Manual_Move]
gcode:
  {% set pos = params.POS|int %}
  {% set travel_speed = params.SPEED|default(100)|int %}
  {% set travel_acc = params.ACC|default(1000)|int %}
  _check_single_motor
  {% set motornum = printer["gcode_macro _dockslide_variables"].motornum %}
  {% if motornum == 2 %}
    MANUAL_STEPPER STEPPER=motor_right MOVE={pos} SPEED={travel_speed} SYNC=0 ACCEL={travel_acc}
    MANUAL_STEPPER STEPPER=motor_left MOVE={pos} SPEED={travel_speed} SYNC=1 ACCEL={travel_acc}
  {% else %}
    MANUAL_STEPPER STEPPER=motor_right MOVE={pos} SPEED={travel_speed} SYNC=1 ACCEL={travel_acc}
  {% endif %}

[gcode_macro Dockslide_Park]
gcode:
  {% set dockvar = printer["gcode_macro _dockslide_variables"] %}
  {% set travel_speed = dockvar.travel_speed %}
  {% set move_pos = dockvar.park_height %}
  {% set travel_acc = dockvar.travel_acc %}
  {% set motornum = dockvar.motornum %}
  {% if dockvar.moving_gantry %}
    {% set move_pos = move_pos + printer.toolhead.position.z %}
  {% endif %}
  {% if tool_approachlocation_z == 0 %}
    {% if motornum == 2 %}
      MANUAL_STEPPER STEPPER=motor_right MOVE={move_pos} SPEED={travel_speed} SYNC=0 ACCEL={travel_acc} # STOP_ON_ENDSTOP=1
      MANUAL_STEPPER STEPPER=motor_left MOVE={move_pos} SPEED={travel_speed} SYNC=1 ACCEL={travel_acc} # STOP_ON_ENDSTOP=1
    {% else %}
      MANUAL_STEPPER STEPPER=motor_right MOVE={move_pos} SPEED={travel_speed} SYNC=1 ACCEL={travel_acc} # STOP_ON_ENDSTOP=1
    {% endif %}
  {% else %}
    {% if motornum == 2 %}
      MANUAL_STEPPER STEPPER=motor_right MOVE={move_pos} SPEED={travel_speed} SYNC=0 ACCEL={travel_acc} # STOP_ON_ENDSTOP=1
      MANUAL_STEPPER STEPPER=motor_left MOVE={move_pos} SPEED={travel_speed} SYNC=1 ACCEL={travel_acc} # STOP_ON_ENDSTOP=1
    {% else %}
      MANUAL_STEPPER STEPPER=motor_right MOVE={move_pos} SPEED={travel_speed} SYNC=1 ACCEL={travel_acc} # STOP_ON_ENDSTOP=1
    {% endif %}
  {% endif %}
  SET_GCODE_VARIABLE MACRO=_dockslide_variables VARIABLE=dockslide_status VALUE=1

[gcode_macro Dockslide_Deploy]
gcode:
  {% set position_y = printer.toolhead.position.y %}
  {% set position_z = printer.toolhead.position.z %}
  {% set dockvar = printer["gcode_macro _dockslide_variables"] %}
  {% set travel_speed = dockvar.travel_speed %}
  {% set travel_acc = dockvar.travel_acc %}
  {% set move_pos = dockvar.deploy_height %}
  {% set safe_y = dockvar.safe_y %}
  {% set safe_z = dockvar.safe_z %}
  {% set front_dock = dockvar.front_dock %}
  {% set motornum = dockvar.motornum %}
  {% if dockvar.flying_gantry %}
    {% set move_pos = printer.toolhead.position.z - deploy_offset %}
  {% endif %}
  {% set tool_approachlocation_z = printer["gcode_macro _btc_Variables"].tool_approachlocation_z %}
  {% if (position_y < safe_y and front_dock) or (position_y > safe_y and not front_dock) %}
    { action_respond_info("Dockslide: Unable to deploy Dockslide, cannot clear safe_y!") }
  {% else %}
  {% set new_position_z = printer.toolhead.position.z %}
    {% if position_z < safe_z %}
      G0 Z{safe_z}
      {% set new_position_z = safe_z %}
    {% endif %}
    {% if dockvar.flying_gantry %}
      {% set move_pos = new_position_z - deploy_offset %}
    {% endif %}
    {% if tool_approachlocation_z == 0 %}
      {% if motornum == 2 %}
        MANUAL_STEPPER STEPPER=motor_right MOVE={move_pos} SPEED={travel_speed} SYNC=0 ACCEL={travel_acc}
        MANUAL_STEPPER STEPPER=motor_left MOVE={move_pos} SPEED={travel_speed} SYNC=1 ACCEL={travel_acc}
      {% else %}
        MANUAL_STEPPER STEPPER=motor_right MOVE={move_pos} SPEED={travel_speed} SYNC=1 ACCEL={travel_acc}
      {% endif %}
    {% else %}
      {% if motornum == 2 %}
        MANUAL_STEPPER STEPPER=motor_right MOVE={move_pos} SPEED={travel_speed} SYNC=0 ACCEL={travel_acc}
        MANUAL_STEPPER STEPPER=motor_left MOVE={move_pos} SPEED={travel_speed} SYNC=1 ACCEL={travel_acc}
      {% else %}
        MANUAL_STEPPER STEPPER=motor_right MOVE={move_pos} SPEED={travel_speed} SYNC=1 ACCEL={travel_acc}
      {% endif %}
    {% endif %}
    SET_GCODE_VARIABLE MACRO=_dockslide_variables VARIABLE=dockslide_status VALUE=2
  {% endif %}

[gcode_macro _Dockslide_Wipe]
gcode:
  {% set direction = params.DIRECTION|default(1)|int %}
  {% set travel_speed = params.FEEDRATE|default(600)|int %}
  {% set dockvar = printer["gcode_macro _dockslide_variables"] %}
  {% set travel_acc = dockvar.travel_acc %}
  {% if direction > 0 %} # Dock at rear
    {% set move_pos1 = dockvar.deploy_height - 15 %}
    {% set move_pos2 = dockvar.deploy_height - 2 %}
  {% else %}
    {% set move_pos1 = dockvar.deploy_height + 15 %}
    {% set move_pos2 = dockvar.deploy_height + 2 %}
  {% endif %}
  {% set motornum = dockvar.motornum %}
  {% if motornum == 2 %}
    MANUAL_STEPPER STEPPER=motor_right MOVE={move_pos1} SPEED={travel_speed} SYNC=0 ACCEL={travel_acc}
    MANUAL_STEPPER STEPPER=motor_left MOVE={move_pos1} SPEED={travel_speed} SYNC=1 ACCEL={travel_acc}
    MANUAL_STEPPER STEPPER=motor_right MOVE={move_pos2} SPEED={travel_speed} SYNC=0 ACCEL={travel_acc}
    MANUAL_STEPPER STEPPER=motor_left MOVE={move_pos2} SPEED={travel_speed} SYNC=1 ACCEL={travel_acc}
    MANUAL_STEPPER STEPPER=motor_right MOVE={move_pos1} SPEED={travel_speed} SYNC=0 ACCEL={travel_acc}
    MANUAL_STEPPER STEPPER=motor_left MOVE={move_pos1} SPEED={travel_speed} SYNC=1 ACCEL={travel_acc}
    MANUAL_STEPPER STEPPER=motor_right MOVE={move_pos2} SPEED={travel_speed} SYNC=0 ACCEL={travel_acc}
    MANUAL_STEPPER STEPPER=motor_left MOVE={move_pos2} SPEED={travel_speed} SYNC=1 ACCEL={travel_acc}
  {% else %}
    MANUAL_STEPPER STEPPER=motor_right MOVE={move_pos1} SPEED={travel_speed} SYNC=1 ACCEL={travel_acc}
    MANUAL_STEPPER STEPPER=motor_right MOVE={move_pos2} SPEED={travel_speed} SYNC=1 ACCEL={travel_acc}
    MANUAL_STEPPER STEPPER=motor_right MOVE={move_pos1} SPEED={travel_speed} SYNC=1 ACCEL={travel_acc}
    MANUAL_STEPPER STEPPER=motor_right MOVE={move_pos2} SPEED={travel_speed} SYNC=1 ACCEL={travel_acc}
  {% endif %}
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

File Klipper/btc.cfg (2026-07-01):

[include ./btc_variables.cfg]  # Required

[input_shaper]                 # Required for input shaper, do not delete

[gcode_macro _UPDATE_FRONTEND]
gcode:
  # Somehow SET_GCODE_VARIABLE is case sensitive.
  # Since Fluidd is using a lowercase Tx macro name,
  # we need to use lowercase names, too.
  {% set tool_current_asperbtc = printer["gcode_macro _btc_Variables"].tool_current_asperbtc %}
  {% set numoftool = printer["gcode_macro _btc_Variables"].numoftool %}
  {% for toolnumber in numoftool %}
    {% set active = toolnumber == tool_current_asperbtc %}

    {% if "active" in printer["gcode_macro t" ~ toolnumber] %}
      { action_respond_info("Setting tool " ~ toolnumber ~ " active: " ~ active) }
      SET_GCODE_VARIABLE MACRO=t{toolnumber} VARIABLE=active VALUE={active}
    {% endif %}

    {% if printer["gcode_macro _btc_Variables"].btc_enable_spoolman_integration %}
      {% if active and "spool_id" in printer["gcode_macro t" ~ toolnumber] %}
        { action_respond_info("Tool " ~ toolnumber ~ " is active. Active spool is now " ~ printer["gcode_macro t" ~ toolnumber].spool_id) }
        SET_ACTIVE_SPOOL ID={ printer["gcode_macro t" ~ toolnumber].spool_id }
      {% endif %}
    {% endif %}
  {% endfor %}

  {% if printer["gcode_macro _btc_Variables"].btc_enable_spoolman_integration and tool_current_asperbtc == -1 %}
    { action_respond_info("No tool is active; clearing active spool") }
    CLEAR_ACTIVE_SPOOL
  {% endif %}

### start Printer start routine ###
[delayed_gcode start_check_carriage]
initial_duration: 3
gcode:
  {% set numoftool = [] %}
  {% for tools in range(6) %}
    {% if printer["gcode_macro t" + tools|string] is defined %}
      _start_populate_tools TOOLNUMBER={tools}
      { action_respond_info("BTC: Tool %d is defined" % (tools)) }
    {% endif %}
  {% endfor %}
  Check_Carriage
  _start_check_second
  {% if printer["gcode_macro Dockslide_Home"] is defined %}
    { action_respond_info("BTC: Dockslide is in use") }
    SET_GCODE_VARIABLE MACRO=_btc_Variables VARIABLE=use_dockslide VALUE=True
  {% else %}
    { action_respond_info("BTC: Dockslide is not in use") }
  {% endif %}
  {% set base_limit_accel = printer.toolhead.max_accel %}
  {% set base_limit_scv = printer.toolhead.square_corner_velocity %}
  SET_GCODE_VARIABLE MACRO=_btc_Variables VARIABLE=base_limit_accel VALUE={base_limit_accel}
  SET_GCODE_VARIABLE MACRO=_btc_Variables VARIABLE=base_limit_scv VALUE={base_limit_scv}

[gcode_macro _start_populate_tools]
gcode:
  {% set numoftool = printer["gcode_macro _btc_Variables"].numoftool + [params.TOOLNUMBER|int] %}
  SET_GCODE_VARIABLE MACRO=_btc_Variables VARIABLE=numoftool VALUE='{numoftool}'

[gcode_macro _start_check_second]
gcode:
  {% if printer["gcode_macro _btc_Variables"].tool_current_asperbtc == -1 %}
    { action_respond_info("BTC: Carriage has no tool on startup!") }
  {% endif %}
### end Printer start routine ###

### start Check state of carriage ###
[gcode_macro Check_Carriage]
gcode:
  { action_respond_info("BTC: Check carriage start. Setting carriage to NO TOOL") }
  SET_GCODE_VARIABLE MACRO=_btc_Variables VARIABLE=tool_current_asperbtc VALUE=-1
  {% for toolnumber in printer["gcode_macro _btc_Variables"].numoftool %}
    _checkasperbtc TOOLNUMBER={toolnumber}
  {% endfor %}
  _UPDATE_FRONTEND

[gcode_macro _checkasperbtc]
gcode:
  {% if printer["gcode_macro _btc_Variables"].tool_current_asperbtc < 0 %}
    query_probe
    _CHECK_CARRIAGE_SECOND TOOLNUMBER={params.TOOLNUMBER|default(0)|int}
  {% endif %}

[gcode_macro _CHECK_CARRIAGE_SECOND]
gcode:
  {% set toolnumber = params.TOOLNUMBER|default(0)|int %}
  {% set frompickup = params.FROMPICKUP|default(0)|int %}
  {% set toolvar = printer["gcode_macro _Variables_t" + toolnumber|string] %}
  {% set tool_xoffset = toolvar.xoffset|float %}
	{% set tool_yoffset = toolvar.yoffset|float %}
	{% set tool_zoffset = toolvar.zoffset|float %}
  {% set tool_shaperfreq_x = toolvar.shaperfreq_x %}
  {% set tool_shaperfreq_y = toolvar.shaperfreq_y %}
  {% set tool_shapertype_x = toolvar.shapertype_x %}
  {% set tool_shapertype_y = toolvar.shapertype_y %}
  #{% set tool_pressure_advance = toolvar.pressure_advance %}
  #{% set tool_pressure_advance_smooth_time = toolvar.pressure_advance_smooth_time %}
  {% set btcvar = printer["gcode_macro _btc_Variables"] %}
  {% set tool_z_hop = btcvar.btc_z_hop %}
  {% set inc_leds = btcvar.btc_inc_leds %}
  {% set tool_zoffset = toolvar.zoffset %}
  {% set z_adjust = btcvar.gcode_offset_z_adjust %}
  {% set tool_approachlocation_z = btcvar.tool_approachlocation_z %}

  {% set toolatcarriage = False %}
  {% if btcvar.carriage_sense_switch and printer["gcode_button carriagesense_t" + toolnumber|string].state == "PRESSED" %}
    {% set toolatcarriage = True %}
	status_active_tool{toolnumber}
    Nozzle_Led{toolnumber}
  {% elif not btcvar.carriage_sense_switch and not printer.probe.last_query %}
    {% set toolatcarriage = True %}
	status_active_tool{toolnumber}
    Nozzle_Led{toolnumber}
  {% endif %}
  {% if toolatcarriage %}
    { action_respond_info("BTC: T%d at carriage" % (toolnumber)) }
    SET_GCODE_VARIABLE MACRO=_btc_Variables VARIABLE=tool_current_asperbtc VALUE={toolnumber}
    {% if frompickup == 1 %}
      status_active_tool{toolnumber}
	  Nozzle_Led{toolnumber}
    {% endif %}
    {% if toolnumber == 0 %}
      ACTIVATE_EXTRUDER EXTRUDER=extruder
    {% else %}
      ACTIVATE_EXTRUDER EXTRUDER=extruder{toolnumber}
    {% endif %}
    {% if 'x' in printer.toolhead.homed_axes and 'y' in printer.toolhead.homed_axes %}
      SET_GCODE_OFFSET X={tool_xoffset} Y={tool_yoffset} move=1	#Apply the nozzle XY offset so that printing proceeds smoothly
      {% if tool_approachlocation_z > 0 %}
        SET_GCODE_OFFSET MOVE=1 Z={tool_zoffset} #apply the z offset before loading the new one to ensure no nozzle crash
        SET_GCODE_OFFSET MOVE=1 Z_ADJUST={z_adjust}
        { action_respond_info("BTC: Z offset now %f (adjusted by %f)" % (tool_zoffset, z_adjust)) }
      {% endif %}
    {% endif %}
    SET_INPUT_SHAPER SHAPER_FREQ_X={tool_shaperfreq_x} SHAPER_FREQ_Y={tool_shaperfreq_y} SHAPER_TYPE_X={tool_shapertype_x} SHAPER_TYPE_Y={tool_shapertype_y}
    #SET_PRESSURE_ADVANCE ADVANCE={tool_pressure_advance} SMOOTH_TIME={tool_pressure_advance_smooth_time}
    {% if frompickup == 1 %}
      {% if tool_z_hop != 0 %}
        SAVE_GCODE_STATE NAME=TOOL_ZHOP_STATE
        G91
        G0 Z-{tool_z_hop}
        RESTORE_GCODE_STATE NAME=TOOL_ZHOP_STATE
      {% endif %}
      {% set fanspeed = printer["gcode_macro _btc_Variables"].last_fan_speed|float %}
      {% if fanspeed > 0 %}
        #M106 S{fanspeed}
        M107
        SET_FAN_SPEED FAN=partfan{toolnumber} SPEED={fanspeed|float}
      {% endif %}
      { action_respond_info("BTC: Setting partfan%d to %f" % (toolnumber, fanspeed)) }
    {% endif %}
  {% else %}
    { action_respond_info("BTC: T%d not at carriage" % (toolnumber)) }
    SET_GCODE_VARIABLE MACRO=_btc_Variables VARIABLE=tool_current_asperbtc VALUE=-1
    {% if frompickup == 1 %}
      {% if printer['print_stats'].state == "printing" %}
        { action_respond_info("BTC: Tool %s not detected at carriage!! Pausing print..." % (toolnumber)) }
		status_blink_tool{toolnumber}
        pause
      {% else %}
        { action_raise_error("BTC: Tool %s not detected at carriage!!" % (toolnumber)) }
      {% endif %}
    {% endif %}
  {% endif %}
### end Check state of carriage ###
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

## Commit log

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2024-08-30 Fixed
    1. 1 x Dock magnet changed to 8x5
    2. Toolhead magnet realigned
    3. Carriage Magnet body fixed
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2024-09-11 Fix Magnet Position
    Changed magnet location on Carriage Rear Body for stronger hold on magnet body after toolhead dropoff
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2024-09-18 Fix missing Hole
    Fix missing hole at pin location
2024-09-27 Added Bom and file fixes
    Added BOM and minor file fixes and updates
    [Lineux Vzbot Bom.xlsx]
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2024-10-10 Fixed check carriage sequence, other minor fixes
    [bashed_macros.cfg, btc.cfg, btc_extras.cfg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]
2024-10-20 Updated design and parts changes
    Updated design
    -Carriage using m5 nuts instead of dowel pins
    -Toolhead using microswitch for carriagesense
    -Dock using threaded dowel pin
    [Dock v35.step, Dock v37.step, Toolhead v18.step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]
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2024-10-21 Fix missing screws
    1. Fix missing screws
    2. Added arrow on carriage body for orientation
    [Vzbot Carriage v34.step, Vzbot Carriage v35.step]
2024-10-22 Added some instructions. Updated btc_nudge for simpler usage
    [btc_nudge.cfg]
2024-10-22 Fixed error
    [btc_nudge.cfg]
2024-11-03 Updated BOM, dock and toolhead
    - Update bom
    - Edit dock and toolhead to use microswitch for docksense
    [Dock v37.step, Dock v46.step, Lineux Vzbot Bom.xlsx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]
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2024-11-04 Revert from git lfs
    [Dock v46.step, Toolhead v26.step, Vzbot Carriage v35.step]
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2024-11-18 Fix spelling
    Spelling fix
    [Back Plate V2 (a).stl, Bambu_Mount.stl, Carriage Body Middle.stl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]
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2024-12-13 Added Parts and Mounts stls and cad
    Added TZ 2.0 + HGX Lite 2.0 Mounts
    Added ebb36 Mount for HGX Lite 2.0
    Update cad
    [Ebb36 HGX Lite 2.0 Mount (1).stl, Ebb36 Spacer HGX Lite.stl, HGX Lite 2.0 Mount.stl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]
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2024-12-16 Fix dimensions offset
    [Carriage Body Middle.stl, Carriage Body Rear.stl]
2024-12-16 Edit missed offsets
    [Carriage Body Front.stl, Carriage Body Rear.stl]
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2024-12-19 Added Bom and updated cad
    Added bom for Lineux One and Lineux DB
    Fix file name of magnet in Lineux One toolhead cad
    Added Umbilical Mount in Lineux One Dock cad
    [Lineux DB Vzbot Bom.xlsx, Lineux One Vzbot Bom.xlsx, Lineux Vzbot Bom.xlsx]
2024-12-20 Added and rearrange files
    Reuploaded full stls for Lineux DB Toolhead
    Fix missing hole for Lineux DB cad
    Reuploaded and sorted by extruders in cad for printed parts
    [Back Plate V2.stl, Back Plate.stl, Bambu_Mount.stl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]
2024-12-20 Added full stls and update cad
    Added full stls for Lineux One Toolhead
    Sort cad for printed parts by extruders
    [Cowl Exo (1).stl, Cowl Exo Klicky.stl, Cowl Goliath.stl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]
2024-12-21 Fix stls
    [Carriage Body Back.stl]
2024-12-21 Fixing files
    [5015 Adapter.stl, 5015 Standoff.stl, Back Plate V2.stl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]
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2024-12-21 Added stls and update cad
    Added stls for WWG2 and Rapido UHF for Lineux DB
    Added stl back plate for beacon cartographer Lineux DB
    Edited voron 2.4 carriage to use switch Lineux DB
    Updated cad for Lineux DB toolhead
    [Back Plate Beacon_cartographer.stl, Carriage Body Back.stl, Carriage Body Front.stl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]
2024-12-22 Fix missing screws
    Added the missing screw
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2024-12-23 Update Lineux One vzbot330 bom
    Update Lineux One vzbot330 bom to include stainless steel solder flux
    [Lineux One Vzbot Bom.xlsx]
2024-12-23 Updated Lineux DB Manual
    Fix microswitch wiring marking
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2024-12-25 Edited and update Lineux One Duct
    Edited Lineux One duct and 5015 adapter
    Updated cad and stls
    [5015 Adapter With standoff.stl, 5015 Adapter.stl]
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2024-12-30 Fix thread pitch Umbilical mount
    Fix thread pitch Umbilical mount
    [Umbilical Extrusion Mount.stl]
2024-12-30 Fix Mgn 12h misaligned holes
    Fix Mgn 12h misaligned holes
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2025-01-02 Update readme, removed btc-klicky
    btc-klicky macros goes inside btc.cfg. Doesn't require to be included
    [btc_klicky.cfg]
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2025-01-07 Fix filename
    [Carriage_Body_A.stl, Carriage_Body_Front.stl, Carriage_Body_Middle.stl]
2025-01-11 Include missing 2 heat inserts
    Included 2 missing heat inserts
    [Lineux One Vzbot Bom.xlsx, Lineux_One_Vzbot_Bom.xlsx]
2025-01-13 Simplified some routine, update klicky routine
    Simplified variables calling
    Better klicky handling
    [btc.cfg, btc_variables.cfg, leds_0.cfg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]
2025-01-13 Fix cooling fan not turning on after toolchange
    [btc.cfg, btc_variables.cfg]
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2025-01-23 Dockslide: Fixed m84 override
    Dockslide
    Fixed m84 override
    Added check status macro
    [btc.cfg, dockslide.cfg]
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2025-02-07 Updated Lineux One Bom and CAD
    Fix m3 dowel support length
    Improved dock rigidity
    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
    [Lineux One Vzbot Bom.xlsx]
2025-02-08 Fix dockslide, initial support for LIP
    [btc.cfg, btc_lip.cfg, dockslide.cfg]
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2025-02-16 Dockslide add firmware_restart override, BTC prepare to use klipper built-in led control
    [btc.cfg, dockslide.cfg]
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2025-02-22 BTC: rework dock move calculation
    dock location is now set in tool_*.cfg files
    uses lock_relative_x_move to calculate aproach, lock and unlock
    positions
    [btc.cfg, btc_variables.cfg, tool_0.cfg]
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2025-03-11 Added extra magnet hole
    Added extra magnet hole on carriage and backplate for those facing issues with too strong magnets affecting the hotend fan for Lineux One
    [Back Plate.stl, Back_Plate.stl, Locking Plate.stl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]
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2025-03-24 Fix renaming stl
    Fix renaming stl
    [Back_Plate.stl, Locking_Plate.stl]
2025-03-24 Added/Updated cad and stl
    Fix duct connector lip to enable 2 wall during print
    Added Voron Trident carriage stl
    [5015_Adapter.stl, 5015_Adapter_MGN12H.stl, 5015_Adapter_With_Standoff.stl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]
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2025-03-30 Create endstops.cfg
    revised to eliminate errors occurring when calibrating bed_mesh
    [endstops.cfg]
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2025-04-18 Added HGX Lite 2.0 V6 Hotend
    Added HGX Lite 2.0 Mount for V6 hotend.
    [HGX_Lite_2.0_V6_Mount.stl, Hgx_Lite_2.0_Mount_V6.stl]
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2025-04-24 btc_nudge: Add configurable movement delay for preventing TTC errors
    [btc_nudge.cfg]
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2025-05-23 Added initial support for Lineux Sling
    1. Initial Lineux Sling support
    2. Added option to use a single driver for dockslide
    3. Added additional routine after initial senses check, whether in print. If in print, to pause, else throw an error to halt
    [btc.cfg, btc_variables.cfg, dockslide.cfg]
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2025-05-23 Fixed Sling pickup/dropoff issues
    Sling needs z offset to be 0 before performing pickup and dropoff
    [btc.cfg]
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2025-06-09 Reset toolchange limits to printer limits
    [btc.cfg, btc_variables.cfg]
2025-06-17 Populate included tools
    Populate included tools at startup. This prevent accidental pickup of not included tools
    [btc.cfg, btc_variables.cfg]
2025-06-27 Includes moved to btc_variables
    No more user editable stuffs at btc.cfg. User edits at btc_variables.cfg and tool_x.cfg only
    [btc.cfg, btc_variables.cfg]
2025-06-28 Fix dockslide unable to return nozzle to printing height
    [btc.cfg, btc_variables.cfg, dockslide.cfg]
2025-06-29 Fix homing when printer started with tool other than T0
    [btc.cfg]
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2025-07-25 Dock changes
    - enlarge dowel hole to 4mm for better clearance
    - lower bambu brush by 1mm
    [(a)_drip_tray.stl, dock.stl, nozzle_blocker_mount.stl]
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2025-08-03 Fix belt tensioner position
    [carriage_a.stl]
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2025-09-12 Added backplate for din1587 cap nuts
    Added backplate for din1587 cap nuts
    [[a]_backplate din 1587.stl]
2025-09-16 Fix cowl trim alignment
    Fix cowl trim alignment
    [[a]_cowl_trim.stl, cowl.stl]
2025-09-18 Fix mesh
    Fix mesh
    [carriage_bottom.stl, carriage_top.stl]
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2025-09-24 Fix dimension carriage top mgn 9h
    Fix dimension carriage top mgn 9h
    [carriage_top_mgn9h.stl]
2025-09-24 Fix 5015 adapter lip
    Fix 5015 adapter lip
    [5015_adapter.stl, 5015_adapter_mgn12h.stl, 5015_adapter_mgn9c.stl]
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2025-10-13 Fix Hotend Mount screw length clearance
    Fix Hotend Mount screw length clearance
    [orbiter2.0_revo voron_plate.stl, orbiter2.0_sailfish_plate.stl, orbiter2.0_td6s_plate.stl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]
2025-10-21 Fixed middle tab
    Fixed middle tab for smaller extrusion gap.
    [dock.stl]
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2025-11-14 create status led wire channel
    create status led wire channel to hotend mount
    [orbiter2.0_chcpro_plate.stl, orbiter2.0_revo voron_plate.stl, orbiter2.0_sailfish_plate.stl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]
2025-11-29 Fix missing screw name
2025-12-27 Fix magnet naming
    Fix magnet naming
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2026-01-18 updated duct alignment and design
    updated duct alignment and design
    updated magnet helper
    [Magnet Mounting Tool.stl, duct_logo.stl, logo_duct.stl]
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2026-01-29 Fix missing screw
    Fix missing screw
    [vzbot_carrier_left.stl, vzbot_carrier_right_top.stl]
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2026-01-31 Added bushing seat tolerance
    [bushing_seat_bottom_x2.stl, bushing_seat_top_left.stl, bushing_seat_top_right.stl]
2026-02-02 Updates
    Added orbiter and rapido for r2t and eva
    Added beacon/carto probe mounts for r2t
    alignment fixes
    [[a]_beacon_mount_beacon_trim.stl, [a]_beacon_mount_carto_trim.stl, [a]_beacon_mount_lineux_trim.stl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]
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2026-02-03 Fix extra tab
    [vzbot_carrier_left.stl]
2026-02-04 Fix bom naming
    [Lineux Stealth r2t Bom.xlsx]
2026-02-10 Uploaded manuals and fixes
    Added dock wire channel
    Added wiring for carriages and toolhead
    Added cable tie slot printed carriage
    Revert to 2 piece carrier vzbot
    Added cable tie slot
    Added build guide
    [carriage_back.stl, carriage_bottom.stl, carriage_top_mgn12h.stl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]
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2026-02-17 Update tool_1.cfg
    fix speed
    [tool_1.cfg]
2026-02-17 Update btc.cfg
    fix bug
    [btc.cfg]
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2026-02-22 Uodated StealthC bushing seat and duct
    Uodated StealthC bushing seat and duct
    [5015_mount.stl, bushing_seat_bottom_x2.stl, bushing_seat_top_left.stl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]
2026-02-23 Added XY Endstops mounts
    Added XY Endstops mounts for both vzbot and voron
    [5015_mount_x_endstop.stl, x_endstop_mount.stl, x_switch_mount.stl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]
2026-02-23 Added Carriage Back X Endstop
    Added Carriage Back X Endstop if using physical x endstop
    [carriage_back_x_endstop.stl]
2026-02-23 Fix magnet gap
    Fix magnet tab depth on r2t backplate and dock
    Change part fan screw to m3 x 6mm
    Updated r2t bom
    Change screw size on manual
    [Lineux Stealth r2t Bom.xlsx, [a]_backplate_multitool_r2t.stl, [a]_backplate_r2t.stl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]
2026-02-24 Added StealthC CNC Tap toolboard mount
    Added StealthC CNC Tap toolboard mount specific for StealthC on Fysetc CNC Tap
    [stealthc_cnctap_hgxlitev2_ebb36_h36_mount.stl, stealthc_cnctap_hgxlitev2_sht36_mount.stl, stealthc_cnctap_orbiter2.0_ebb36_h36_mount.stl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]
2026-03-01 Added optional screw for strength
    Added optional screw for strength.
    Changes to locking plate and carriage B parts
    [[a]_locking_plate.stl, carriage_b_left.stl, carriage_b_right.stl]
2026-03-02 Fix toolboard mount and cover
    Fix sherpa micro toolboard mount to allow clearance between tools
    Fix toolboard cover to allow clearance between tools
    [(a)_toolboard_cover.stl, sherpa_micro_ebb36_h36_mount.stl, sherpa_micro_sht36_mount.stl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]
2026-03-03 Added Umbilical 90deg Adapter
    Added Umbilical 90deg Adapter
    Added new toolboard cover
    [(a)_logo_UA_90deg.stl, (a)_toolboard_cover.stl, [a]_toolboard_cover.stl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]
2026-03-05 Fix Multitool duct
    Fix Multitool duct
    [[a]_duct_multitool.stl, [a]_duct_vzbot_multitool.stl]
2026-03-06 Fix StealthC Duct and added stealthc Backplate
    Fix StealthC Duct
    Added StealthC Backplate
    [[a]_backplate_stealthc_multitool.stl, duct_multitool.stl, duct_r2t.stl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]
2026-03-06 Fix duct and multitool duct stealthc
    Fix duct and multitool duct stealthc
    [duct_multitool.stl, duct_r2t.stl]
2026-03-07 Edit ptfe path on back cover
    Edit ptfe path on back cover of umbihub
    [umbihub_back_cover.stl]
2026-03-10 Fix r2.1 90deg umbilical adapter
    Fix r2.1 90deg umbilical adapter
    [umbilical_adapter_90deg.stl]
2026-03-11 Fix missing wire channel for docksense
    Fix missing wire channel for docksense
    [stealth_r2t_dock_fysetc_cnc_tap.stl, stealth_r2t_dock_voron_cnc_carriage.stl, stealth_r2t_dock_voron_printed_carriage.stl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]
2026-03-13 fix 6x3mm magnet depth r2t dock
    fix 6x3mm magnet depth r2t dock
    [r2t_dock.stl, stealth_r2t_dock_fysetc_cnc_tap.stl, stealth_r2t_dock_voron_cnc_carriage.stl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]
2026-03-14 Updated lock plate and bushing seat
    Updated lock plate to allow screw cutout and adjusted bushing seat for dome nut clearance
    [bushing_seat_bottom_x2.stl, bushing_seat_top_left.stl, bushing_seat_top_right.stl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]
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2026-04-04 Update tool_1.cfg
    fix wrong naming of tool
    [tool_1.cfg]
2026-04-06 Update dockslide.cfg
    Fix bug
    [dockslide.cfg]
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2026-04-20 Added Ebb36 Gen 2 toolboard cover
    Added Ebb36 Gen 2 toolboard cover
    [(a)_toolboard_cover_ebb36gen2.stl]
2026-04-20 fix: vzbot carriage gif pointing to the wrong file
2026-04-30 Added missing diffuser and led clip
    Added missing diffuser and led clip
    [diffuser.stl, led_clip_x2.stl]
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2026-05-05 Added eddy cowl and tiga bom
    Added eddy cowl
    Added tiga bom
    Added vzbot official cnc dock
    [Lineux Stealth Tiga Bom.xlsx]
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2026-05-10 Added led jig and magnet helper
    Added led jig and magnet helper for Tiga
    [Magnet Helper v9.step, Magnet Helper.stl, lineux_stealth_tiga_a_led_jig.stl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]
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2026-05-21 Edit Magnet Tab to avoid microswitch lever
    Edit Magnet Tab to avoid microswitch lever
    [btc_extras.cfg]
2026-05-24 Update btc.cfg
    Fix Sling mode dropoff missing dockslide park movement
    [btc.cfg]
2026-05-24 Edited Tiga dock and toolhead
    Edited Tiga dock magnet tab.
    Fix alignment of umbilical adapter.
    Shift microswitch position a bit more.
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2026-05-27 Update btc.cfg
    Edit tool_pickup_third for sling mode to apply z offsets after toolchange
    [btc.cfg]
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2026-06-09 Fix hole size in backplate
    Fix hole size in backplate
2026-06-19 Added AAA carrier for fan connection
    Added AAA carrier for fan connection
    [5015_duct_adapter.stl, [a]_carrier_aaa_trim.stl, [a]_carrier_b_left_trim.stl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]
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2026-06-22 Added carriage back for carbon gantry
    Added carriage back for carbon gantry
    Edit carriage bottom for carbon gantry clearance
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2026-06-26 Added mising belt tensioner
    Added missing belt tensioner in stl
    [[a]_belt_tensioner_x2.stl]
2026-06-29 Edited klicky mount for strength
    Edited klicky mount for strength in Tiga toolhead.
    [[a]_belt_tensioner_x2.stl, [a]_klicky_mount.stl]
2026-06-29 Added missing vzbot dockslide belt tensioner
    Added missing vzbot dockslide belt tensioner
    [[a]_belt_tensioner_x2.stl]
2026-06-30 Updated naming Tiga Dock
    Updated naming of Tiga dock
    Added stls for Tiga dock
    [[a]_backplate.stl, [a]_backplate_r2t.stl, [a]_drip_tray.stl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]
